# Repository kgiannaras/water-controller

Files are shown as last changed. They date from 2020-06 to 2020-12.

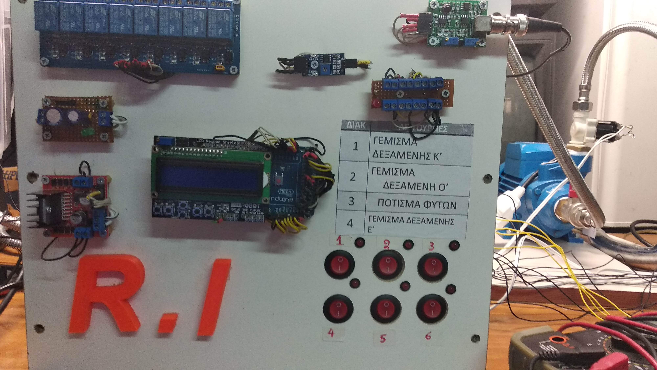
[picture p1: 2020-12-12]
photo/IMG_20200913_190725.jpg

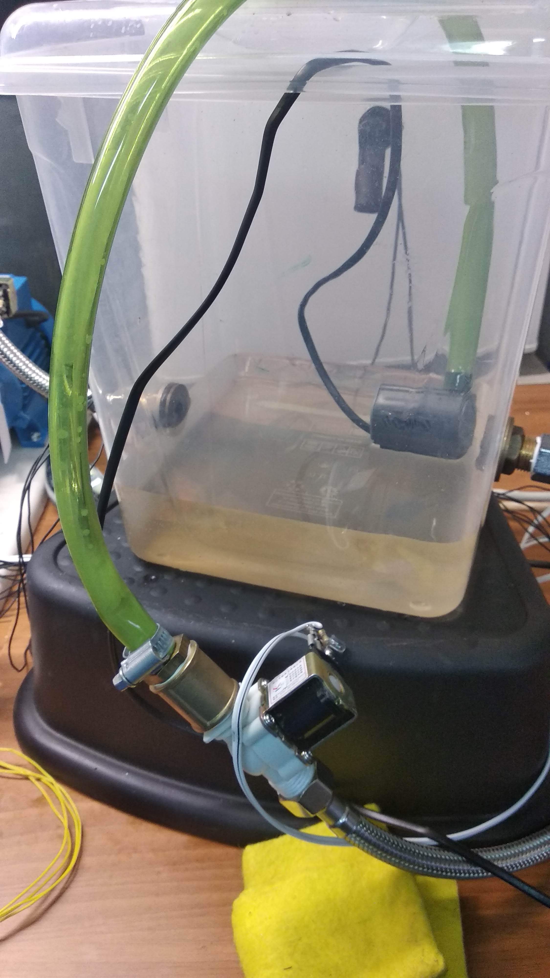
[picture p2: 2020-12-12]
photo/IMG_20200913_191104.jpg

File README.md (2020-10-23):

ΠΕΡΙΛΗΨΗ

Ο σκοπός της ομάδας μας για φέτος, είναι η δημιουργία  ενός συστήματος, το οποίο θα συλλέγει το νερό της βροχής σε μια δεξαμενή και αφού ελέγχει την οξύτητα του, θα το διαχειρίζεται ανάλογα. Αν είναι ακατάλληλο, το αποθηκεύει σε μια δεξαμενή, όπου θα κριθεί από τον κάτοχο το τι θα το κάνει. Ενώ, αν είναι κατάλληλο το νερό,  το αποθηκεύει προς χρήση είτε μέσω των διασωληνώσεων του σπιτιού(π.χ θερμοσίφωνας, βρύση,κ.λ.π), είτε μέσω μιας διασωλήνωσης, για άλλου είδους χρήση. Στην δική μας περίπτωση, το κατάλληλο νερό, το αξιοποιήσαμε σε κάτι που θεωρούμε πολύ σημαντικό, την αστική γεωπονία. Το σύστημα που προτείνουμε έχει ως κύρια πλεονεκτήματα την εξοικονόμηση από 30 έως 50 τις εκατό του πόσιμου νερού με οικονομικό, αλλά και περιβαντολλογικό όφελος και στην περίπτωση της αστικής καλλιέργειας προσφέρει την βέλτιστη ανάπτυξη των φυτών και είναι ό,τι καλύτερο όσον αφορά την αστική γεωπονία.Τα υλικά που θα χρησιμοποιήσουμε για την δημιουργία αυτής της κατασκευής, είναι τα παρακάτω:

ΗΛΕΚΤΡΟΝΙΚΑ

1x Arduino Mega                                    23.90 ΕΥΡΩ
1x Σταθεροποιημένο τροφοδοτικό 12V/5A               9.00 ΕΥΡΩ
1x Σταθεροποιημένο τροφ. 12V / 2A                   3.00 ΕΥΡΩ
2x  HC-SR04                                         5.00 ΕΥΡΩ
1x  8 relay                                         4.44 ΕΥΡΩ
1x  D1 ROBOT LCD                                    2.55 ΕΥΡΩ
1x ph sensor    Liquid PH 0-14 Value Detect Sensor 17,00 ΕΥΡΩ      
1x Water level sensor  Tank Pool Horizontal         2,77 ΕΥΡΩ

ΥΔΡΑΥΛΙΚΑ

4x  Ηλεκτροβάνες 12V Solenoid Valve 1/2"  60.00ΕΥΡΩ
3x  Μπιτόνια                              30.90ΕΥΡΩ
3χ βρυσάκια διακοπτης                    12.00 ΕΥΡΩ
2x  Σπιράλ 25cm                           4.00 ΕΥΡΩ
2x  Σπιράλ 60cm                           4.50 ΕΥΡΩ
5x  Μαστοί                               12.50 ΕΥΡΩ
1x teflor                                 0,30 ΕΥΡΩ
Συνολική Αξία:                         191 ,86 ΕΥΡΩ

Αναλυτική περιγραφή όλων των βημάτων υλοποίησης υπάρχουν στην ιστοσελίδα μας
https://openedtech.ellak.gr/robotics2020/sillektis-elegktis-oxinis-vrochis/

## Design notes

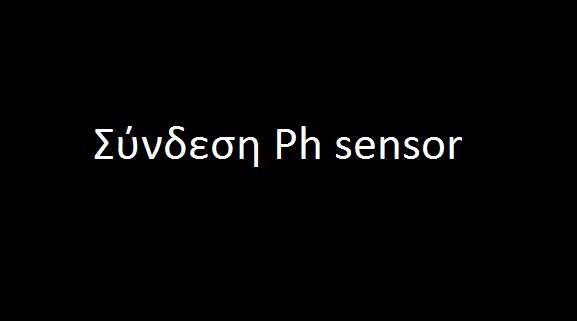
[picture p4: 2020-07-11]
photo/Σύνδεση-Ph-sensor.png

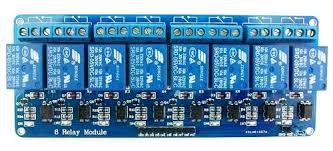
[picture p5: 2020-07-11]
photo/8r.jpg

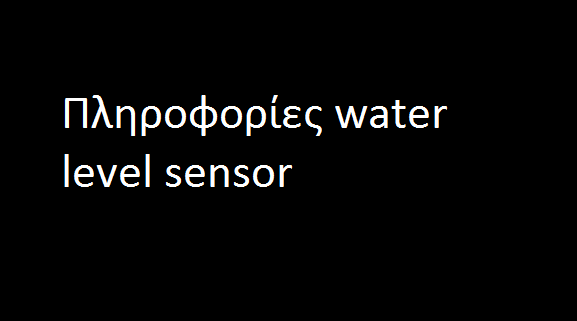
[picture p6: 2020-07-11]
photo/πληροφοριες-water-level.png

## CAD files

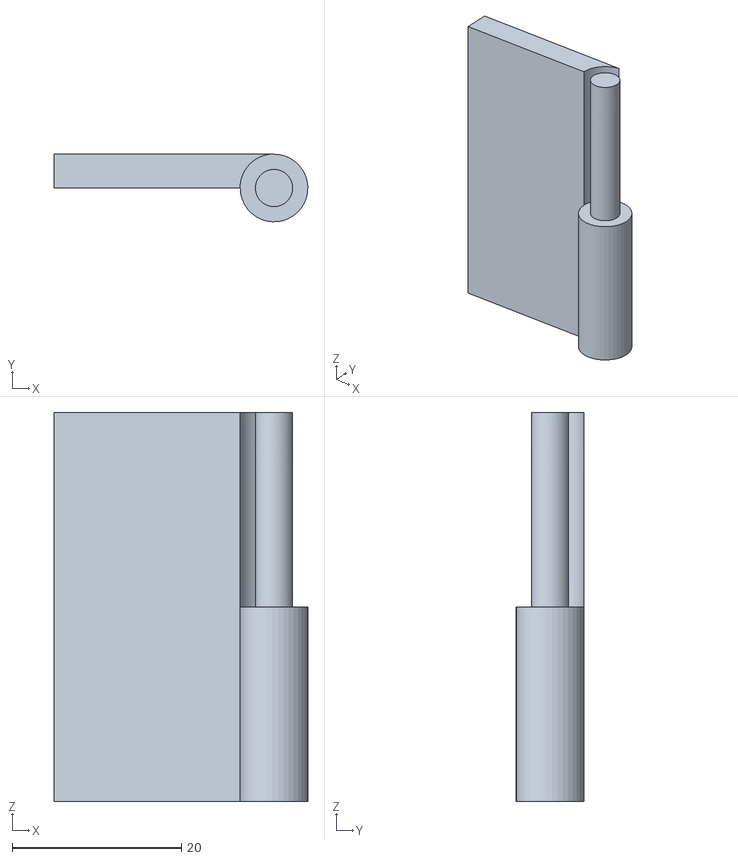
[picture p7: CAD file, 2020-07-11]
stl/hingecomplete.stl
30.0 x 7.99 x 46.0

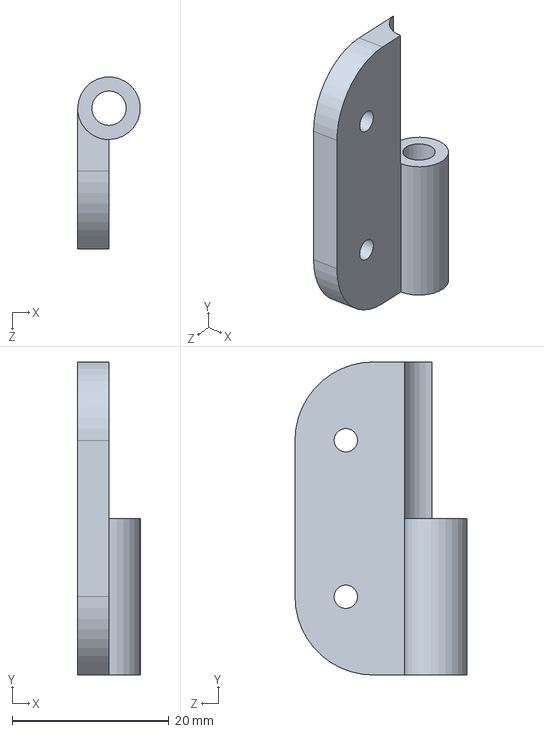
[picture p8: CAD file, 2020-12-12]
123d/Quick_Hinge/long-hinge-pt2.SLDPRT
7.99 x 40.0 x 22.0 mm

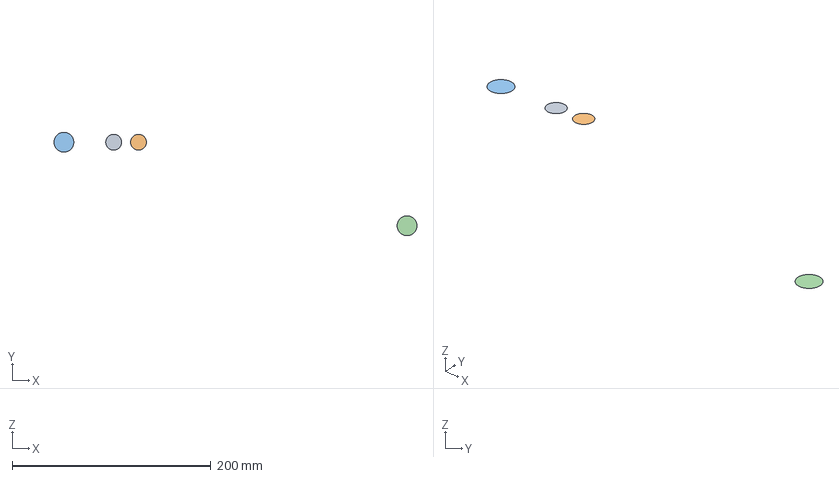
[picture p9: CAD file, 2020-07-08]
freecad/tank_o.FCStd
365.0 x 104.0 x 0 mm
Circle
Circle001
Circle002
Circle003

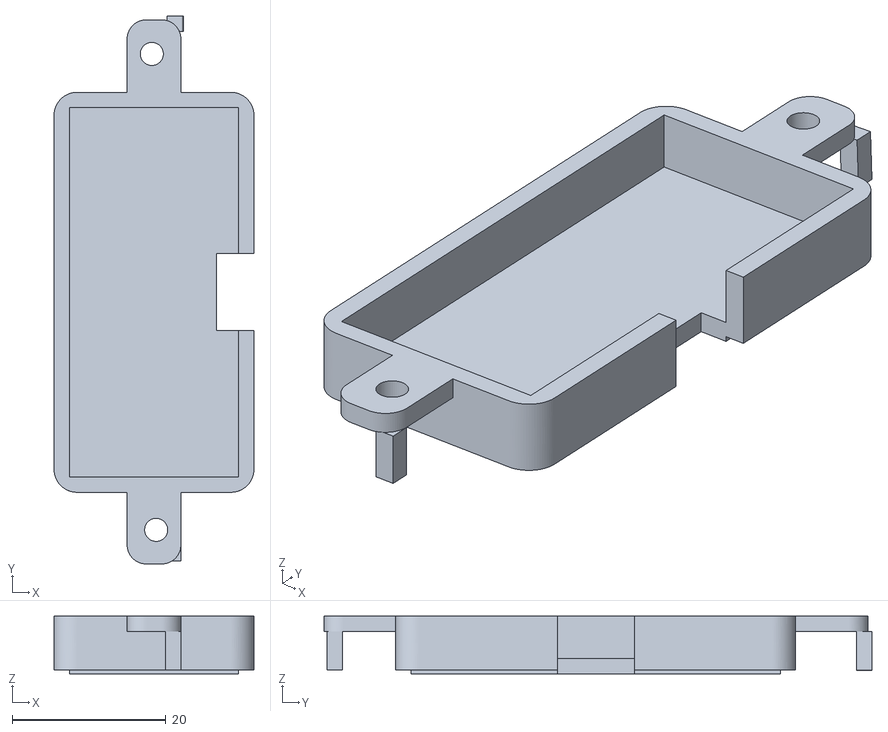
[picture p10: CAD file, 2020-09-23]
stl/hcsr04case.stl
26.0 x 71.2 x 7.50

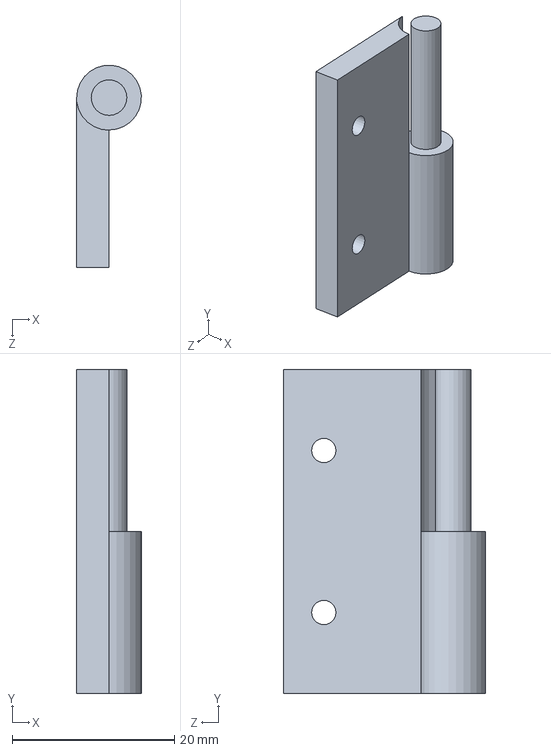
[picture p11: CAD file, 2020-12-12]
123d/Quick_Hinge/long-hinge-pt1.SLDPRT
7.99 x 40.0 x 25.0 mm

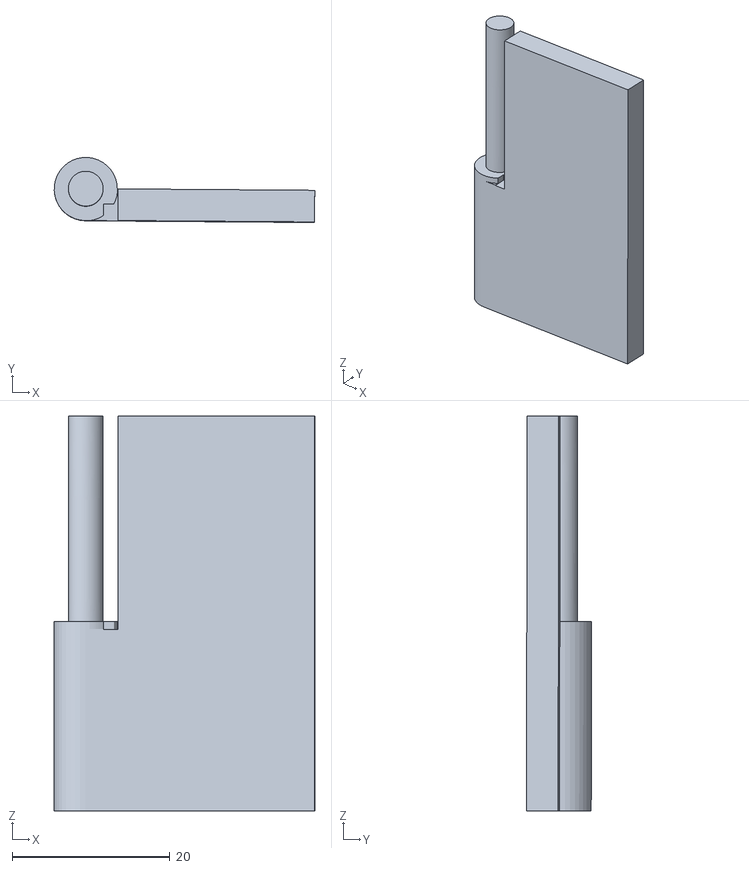
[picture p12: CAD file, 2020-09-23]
stl/hingeall.stl
33.0 x 8.24 x 50.0

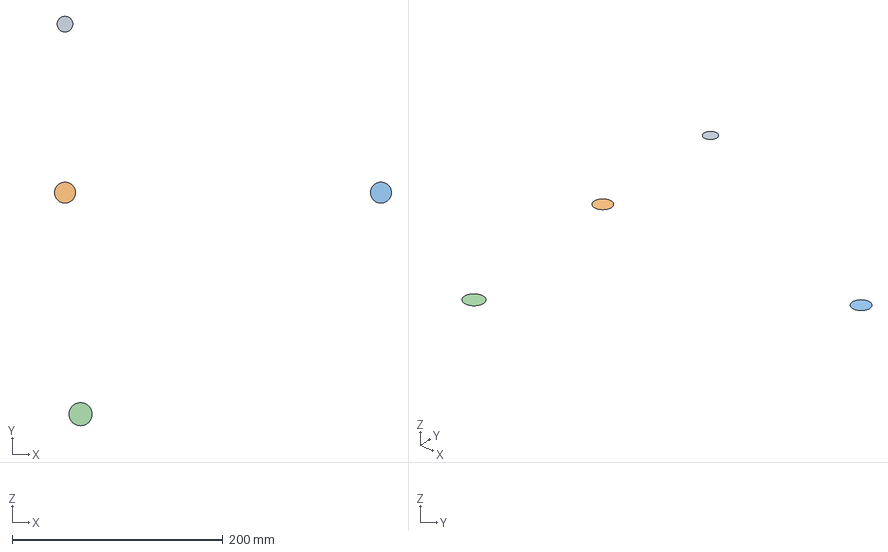
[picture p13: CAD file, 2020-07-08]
freecad/tank_e.FCStd
320.0 x 388.9 x 0 mm
Circle
Circle001
Circle002
Circle003

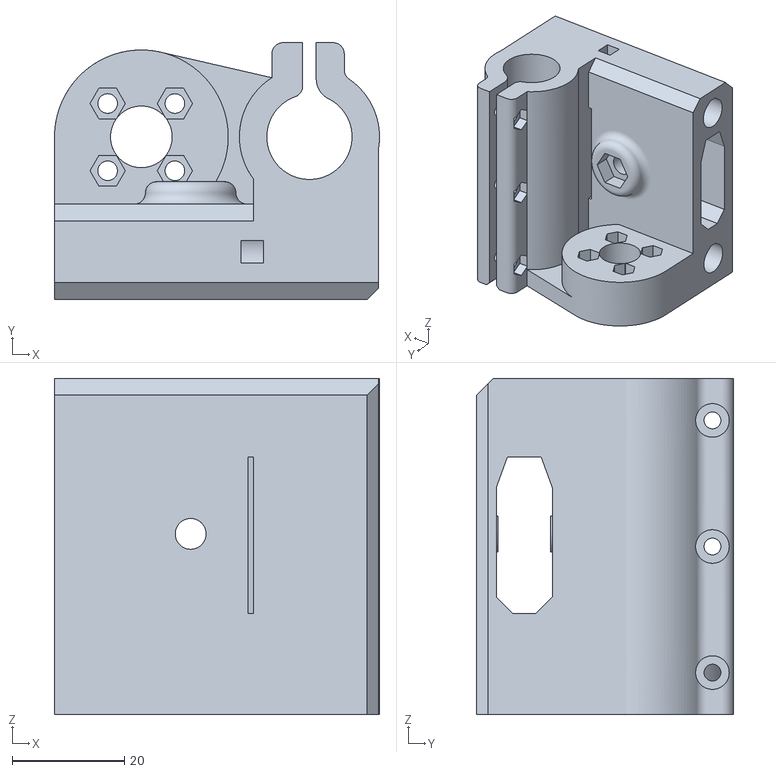
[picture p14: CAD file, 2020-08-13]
stl/x_end_idler.stl
58.0 x 45.8 x 60.0

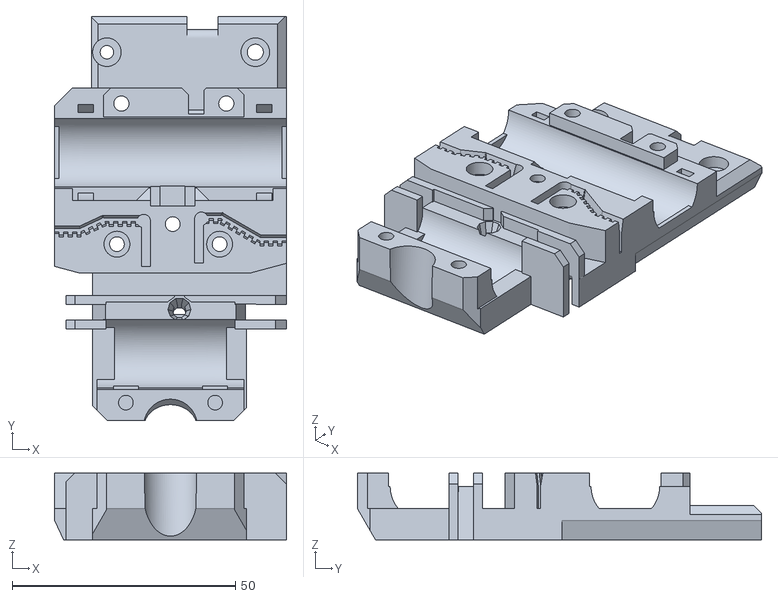
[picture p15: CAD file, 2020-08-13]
stl/X-carriage(R2)-MK3s_MK3s.stl
52.0 x 90.5 x 15.0

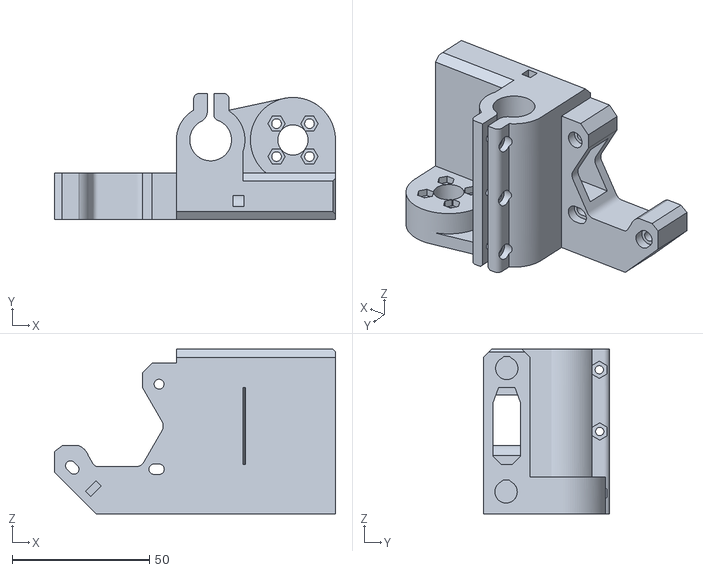
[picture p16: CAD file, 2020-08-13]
stl/x_end_motor.stl
102.4 x 46.0 x 60.0

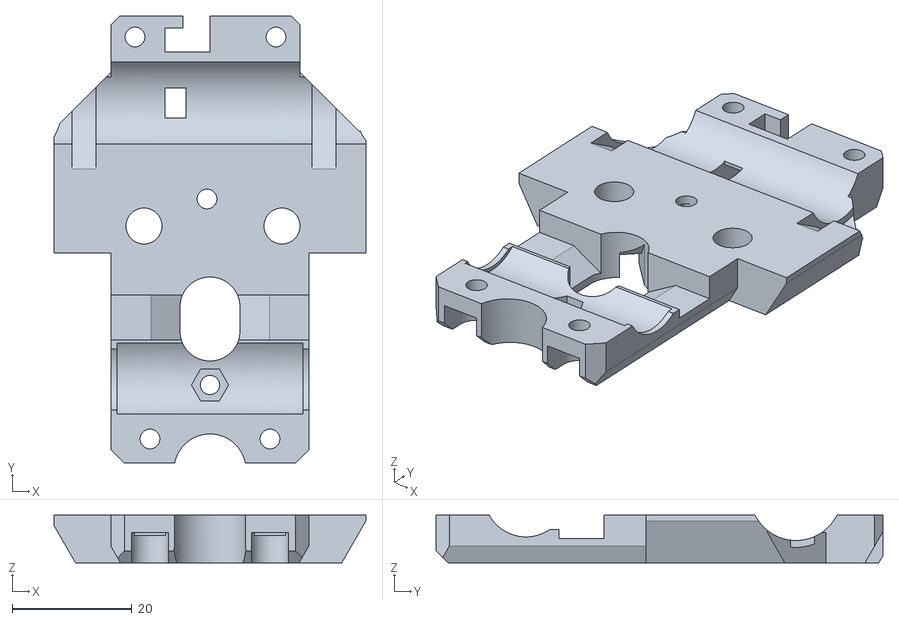
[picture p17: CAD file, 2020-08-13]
stl/Prusa X-Carriage Rear (R3).stl
52.0 x 74.5 x 8.00

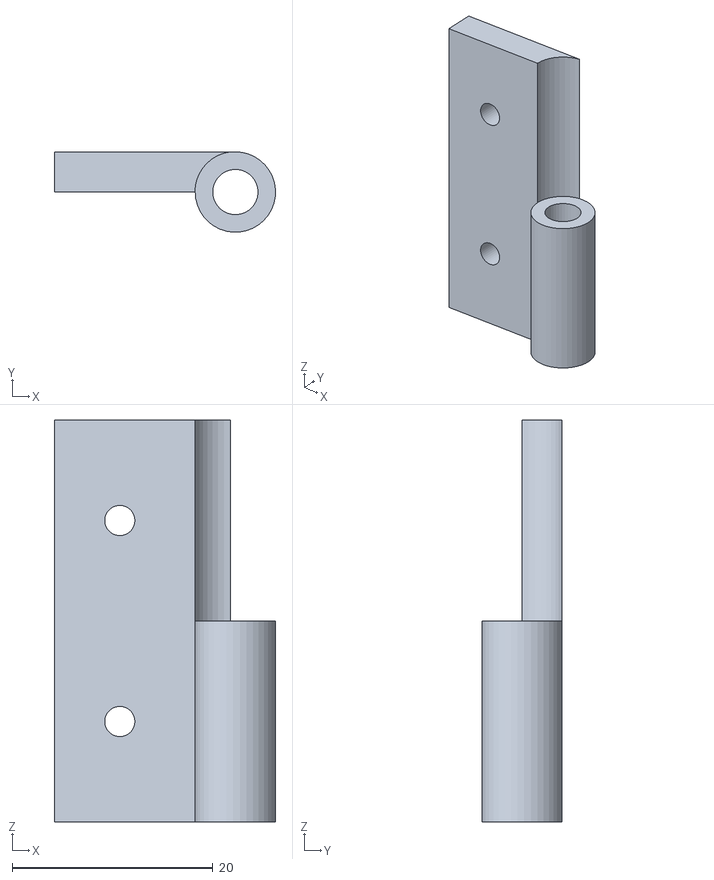
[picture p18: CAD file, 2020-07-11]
stl/long-hinge-pt2.STL
22.0 x 7.99 x 40.0

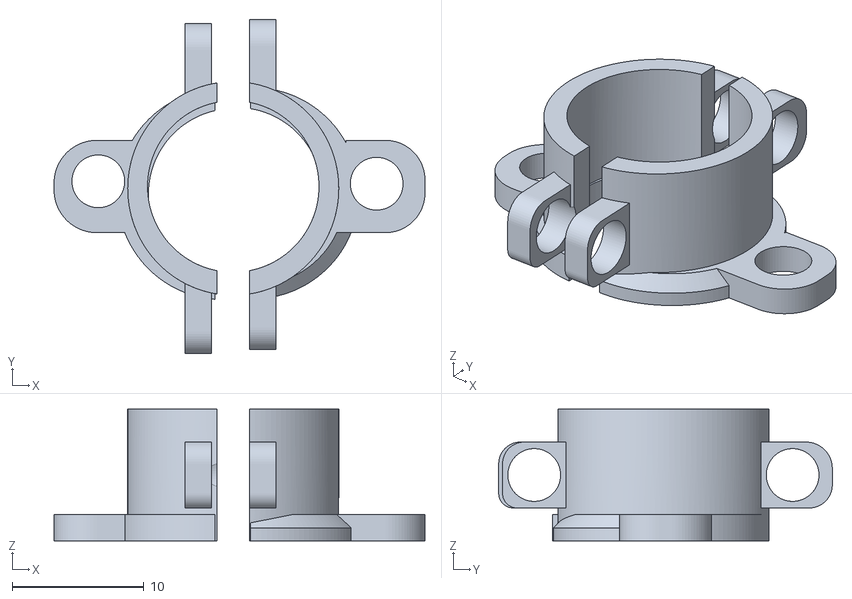
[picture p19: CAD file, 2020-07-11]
stl/ringPH.stl
28.1 x 25.3 x 10.0

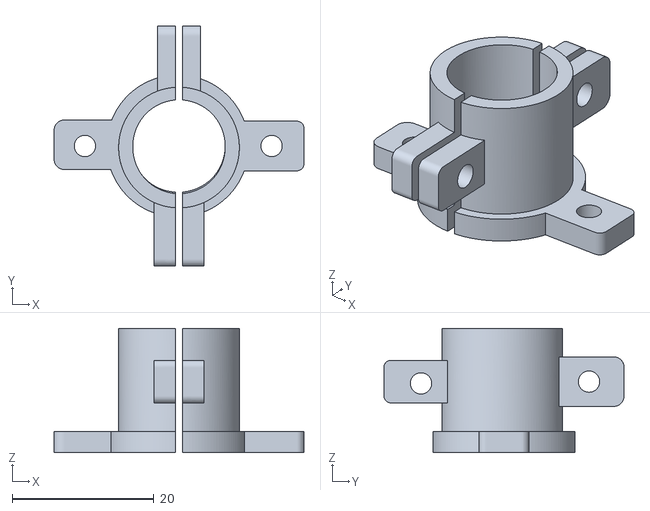
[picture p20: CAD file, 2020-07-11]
stl/ringell2.stl
35.2 x 33.8 x 17.5

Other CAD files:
stl/long-hinge-pt1.STL
stl/hingeup.stl
stl/hingebase.stl

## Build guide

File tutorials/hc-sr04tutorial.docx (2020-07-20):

Δημιουργία θήκης hc-sr04 (εύκολη εκδοχή)

Η θήκη είναι χωρισμένη σε δύο μέρη το καπάκι και την βάση

ΒΑΣΗ

Κατεβάζουμε το αρχείο από την παρακάτω ιστοσελίδα και μόλις το αποσυμπιέσουμε ανοίγουμε το long hinge pt2

Ιστοσελίδα (https://www.thingiverse.com/thing:47591)

Μόλις ανοίξουμε το αρχείο το επιλέγουμε και θα χρησιμοποιήσουμε την εντολή convert mesh to solid που θα μας επιτρέψει να τροποποιούμε το σχήμα γιατί αν δεν χρησιμοποιήσουμε την εντολή αυτή δεν θα μπορέσουμε να κάνουμε τίποτα στο σχήμα.

Με την εντολή sketch rectangle θα φτιάξουμε ένα ορθογώνιο 14mm x 40mm

Με την εντολή extrude υψώνουμε το σχήμα για 4mm .

Με την εντολή move το μετακινούμε εκεί που αρχίζει το ορθογώνιο του μεντεσε

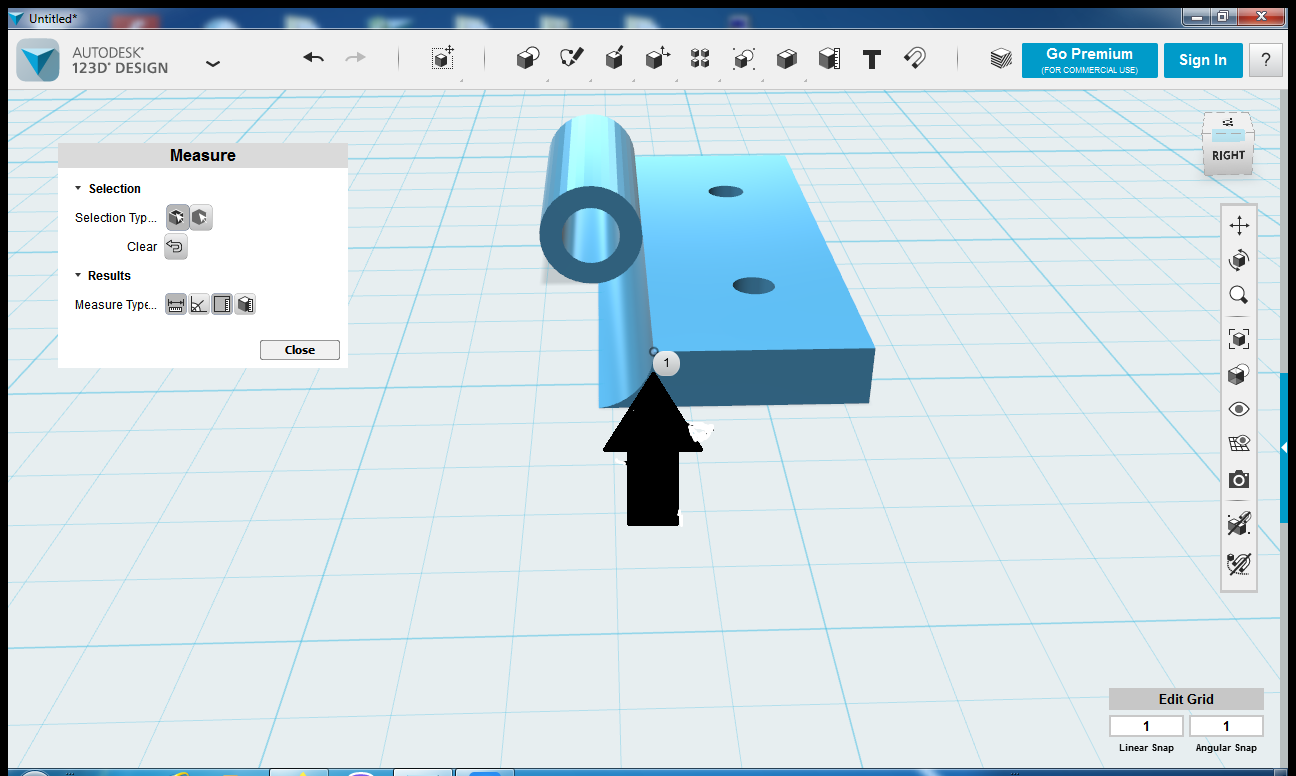
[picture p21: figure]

Έπειτα πηγαίνουμε στις επιλογές στο combine και επιλέγουμε το subtract θα χρειαστούν δυο επιλογές το πρώτο κλικ θα είναι στο το αντικείμενο που θέλουμε να ανοίξουμε την τρύπα και το δεύτερο κλικ στο το δεύτερο αντικείμενο που το σχήμα του θα σχηματίσει την τρύπα στο προηγούμενο αντικείμενο.Αυτό θα το κάνουμε μόνο που αντί για κύβο θα έχουμε τον μεντεσε και κύκλο το ορθογώνιο που φτιάξαμε . Στις επόμενες εικόνες φαίνεται ένα παράδειγμα ενός κύβου από τον οποίο θα αφαιρέσουμε ένα μέρος μιας σφαίρας.

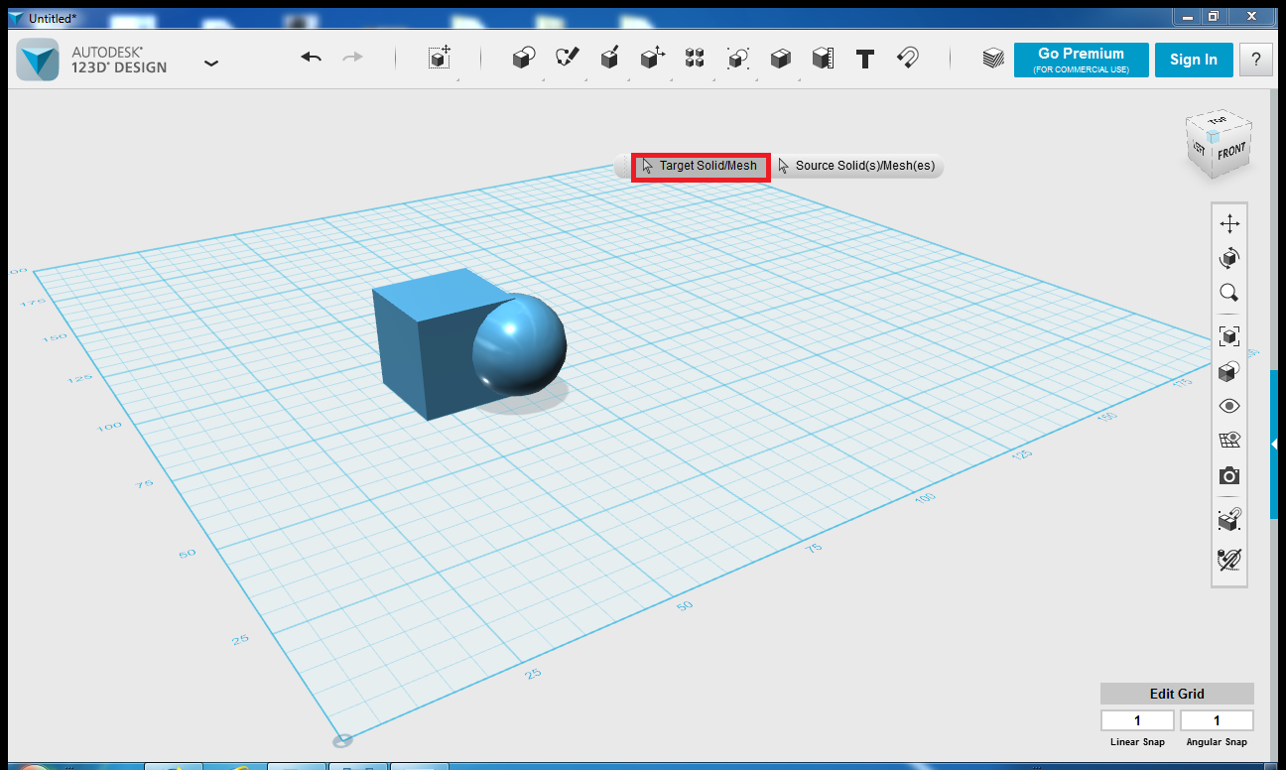
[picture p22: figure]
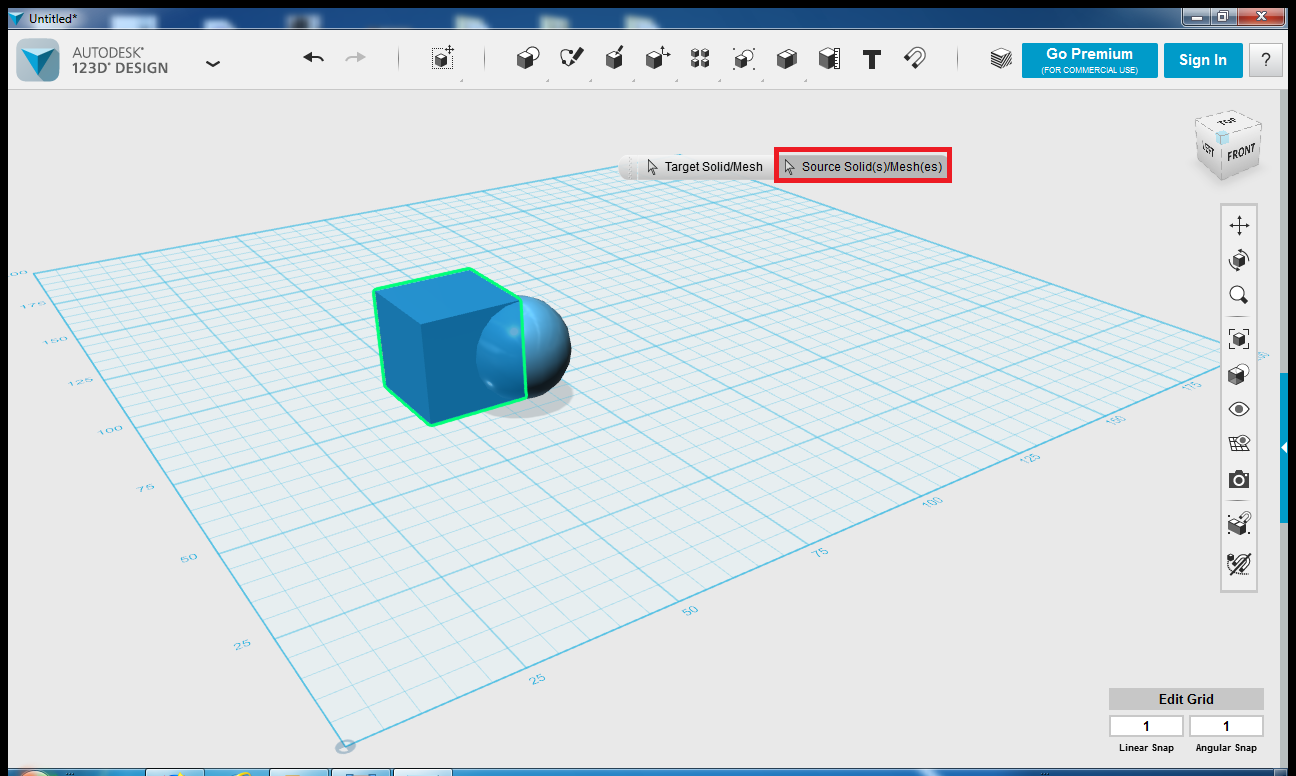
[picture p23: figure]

Στην επόμενη εικόνα φαίνεται το τελικό σχήμα που απέμεινε μετά την αφαίρεση του δεύτερου αντικειμένου

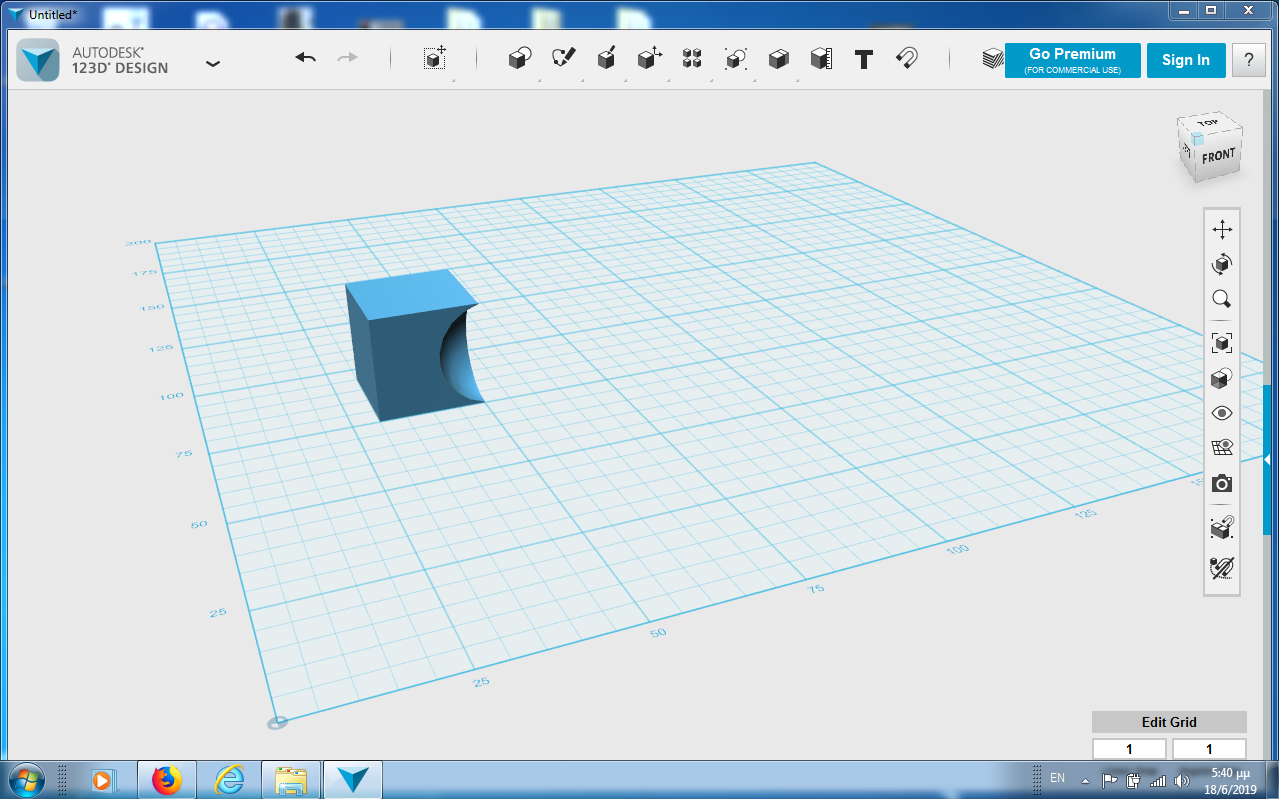
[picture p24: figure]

Μόλις γίνει αυτό να μεγαλώσετε και τις δύο πλευρές εξωτερικά κατά 7mm με το extrude και αν τις μειώσετε εσωτερικά κατά 5mm με το extrude .

Με την εντολή sketch rectangle θα φτιάξουμε δύο ορθογώνια 2mm x 21mm

Με την εντολή extrude υψώνουμε το σχήμα για 4mm .

Με την εντολή move το μετακινούμε στις άκρες του μεντεσε

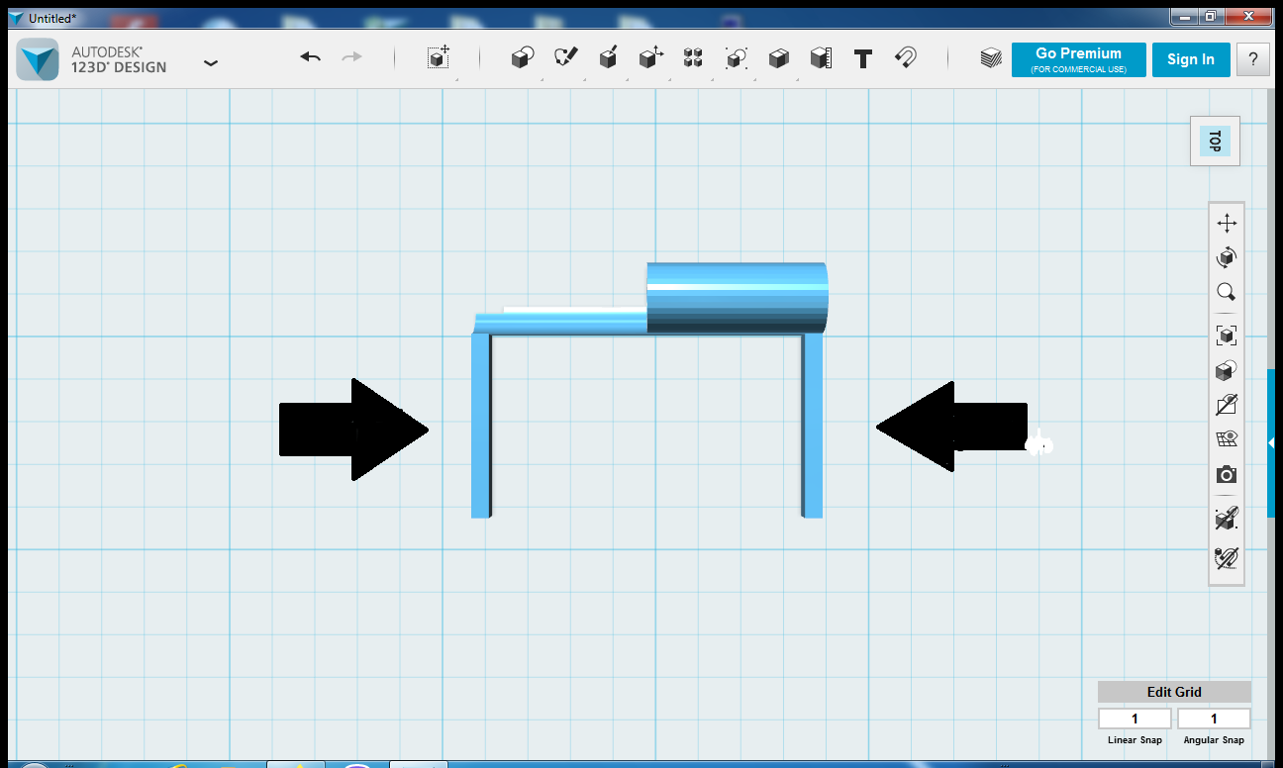
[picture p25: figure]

Στις λειτουργίες combine θα επιλέξουμε το merge και θα επιλέξουμε τα δύο αντικείμενα που θέλουμε να ενώσουμε το ένα ορθογώνιο με τον μεντεσε . Μόλις το κάνουμε ξανακάνουμε merge με το άλλο ορθογώνιο .

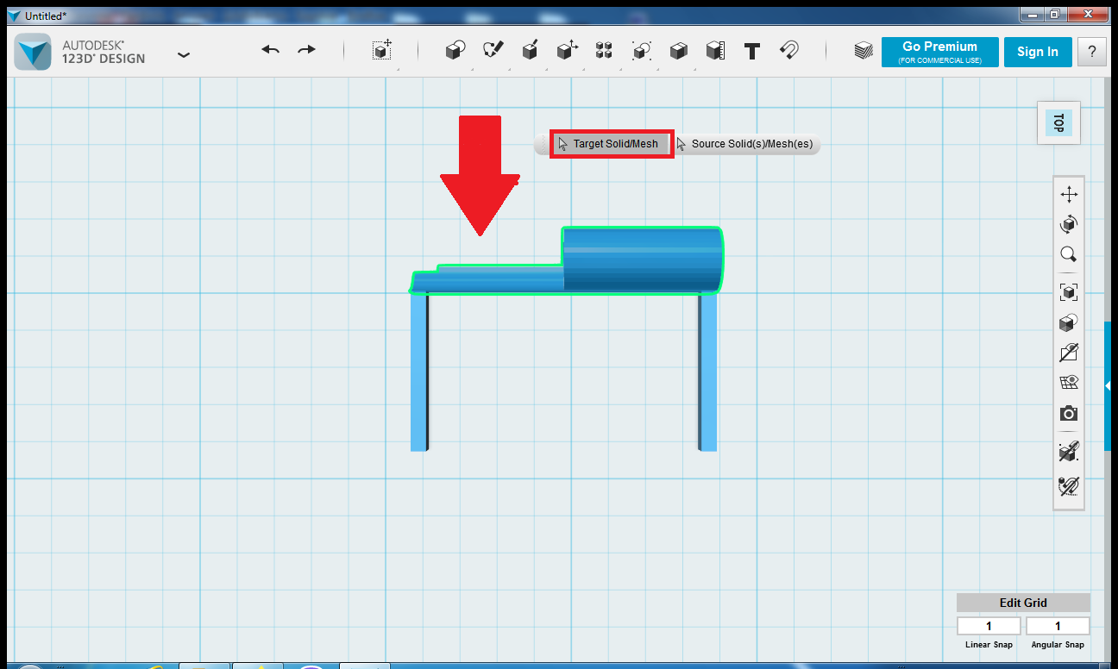
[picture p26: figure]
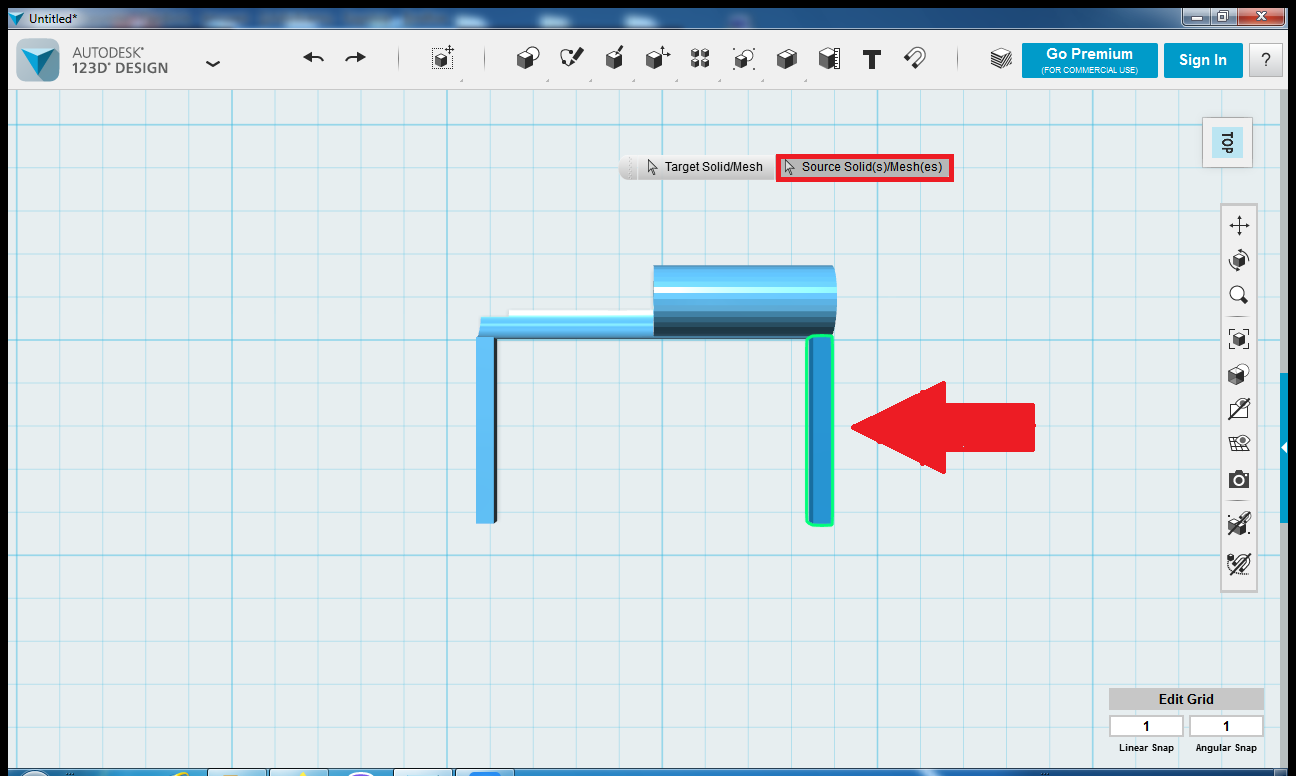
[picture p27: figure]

Με την εντολή sketch rectangle φτιάχνουμε ένα ορθογώνιο 50mm x 4mm

Με την εντολή extrude το υψώνουμε για 4mm .

Με την εντολή move μετακινούμε το ορθογώνιο στην άλλη πλευρά του μεντεσέ και να είναι κάθετος προς τις άλλες δύο πλευρές του μεντεσέ .

Μόλις το κάνετε αυτό θα κάνετε δύο τρύπες με το τρυπάνι των 2mm στα σημεία που δείχνει το αρχείο ώστε να βιδώσουμε την βάση.

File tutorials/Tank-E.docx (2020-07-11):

Δεξαμενή Ε΄

Η δεξαμενή Ε΄είναι η δεξαμενή στη οποία θα γίνεται η συλλογή του βρόχινου νερού και θα ξεχωρίζετε σε καθαρό ή όξινο ανάλογα με το ph.

Παρακάτω ακολουθούν οι πίνακες με τα αναγκαία υλικά και εργαλεία.

Υλικά για αυτό το βήμα | Ποσότητες
Ph sensor | 1
Water level sensor | 1
Μαστοί δεξαμενής | 2
Ηλεκτροβάνες | 2
Σπιράλ 25cm | 2
Σπιράλ 60cm | 2
Βρυσάκι διακόπτης | 2
3d δαχτυλίδι για τον ph | 1

Απαραίτητα εργαλεία για το βήμα αυτό

1) Δράπανο ηλεκτρικό
2) Ποτηροτρύπανο 15mm
3) Ποτηροτρύπανο 20mm
4) Ποτηροτρύπανο 22mm

5)Ποτηροτρύπανο 16mm

6)Κάβουρας για σύσφιξη μαστού

Βήμα 1: 1η πλευρά

Πρώτο βήμα είναι να ασχοληθούμε με την πρώτη πλευρά. Βάση του σχεδίου κάνουμε μία τρύπα 15mm που θα απέχει 50mm από το ανώτερο σημείο της δεξαμενής και θα απέχει 100mm από την αριστερή πλευρά της δεξαμενής. Αυτή η τρύπα θα γίνει χρησιμοποιώντας το ηλεκτρικό δραπανο και το ποτηροτρύπανο των 15mm.

Αν δεν γνωρίζετε τι είναι το ποτηροτρύπανο

Ακολουθεί ενδεικτική εικόνα.

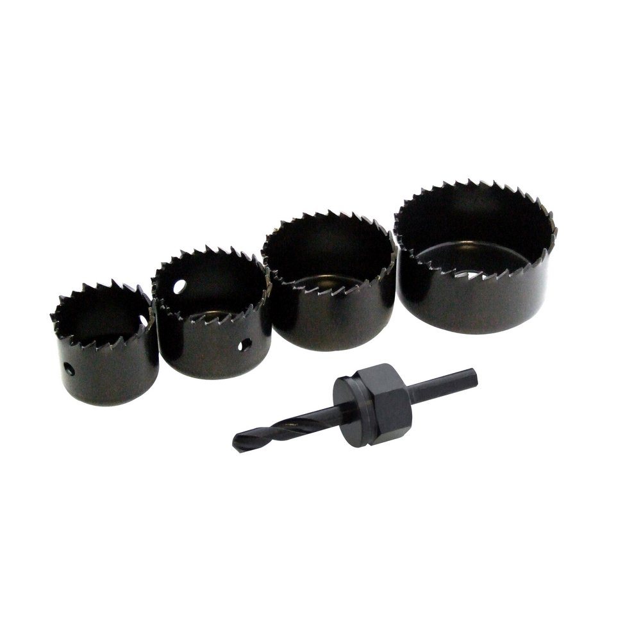
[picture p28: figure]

Εικόνα 1: Ποτηροτρύπανα

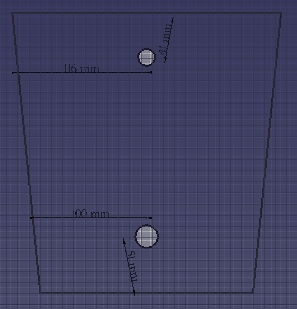
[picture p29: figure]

Εικόνα 2 :Σχέδιο πλευράς 1

Η παρακάτω εικόνα δείχνει το αποτέλεσμα της τρύπας.

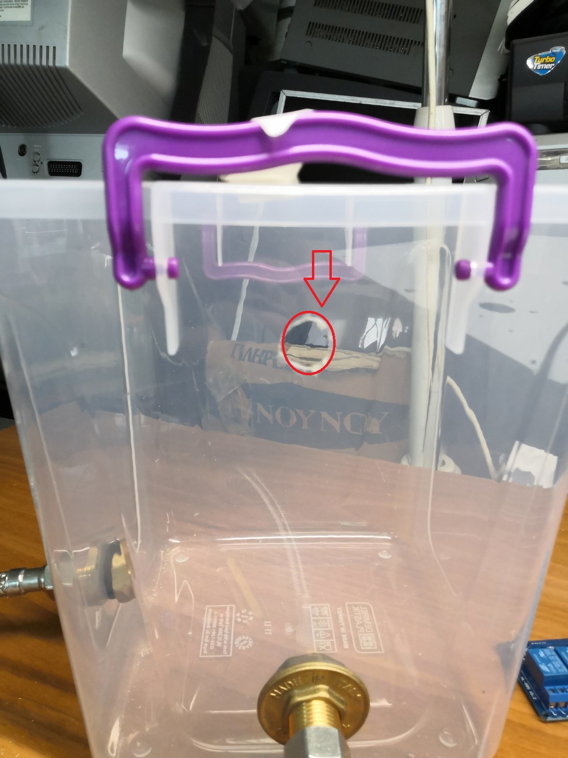
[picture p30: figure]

Εικόνα 3: Αποτέλεσμα τρύπας.

Στην ίδια πλευρά ανοίγουμε βάση του σχεδίου μία τρύπα 20mm που θα απέχει 50mm από την βάση και 100mm από αριστερά για να βάλουμε τον μαστό δεξαμενής. Αυτή η τρύπα θα χρειαστεί το ηλεκτρικό δράπανο και το ποτηροτρύπανο των 20mm.

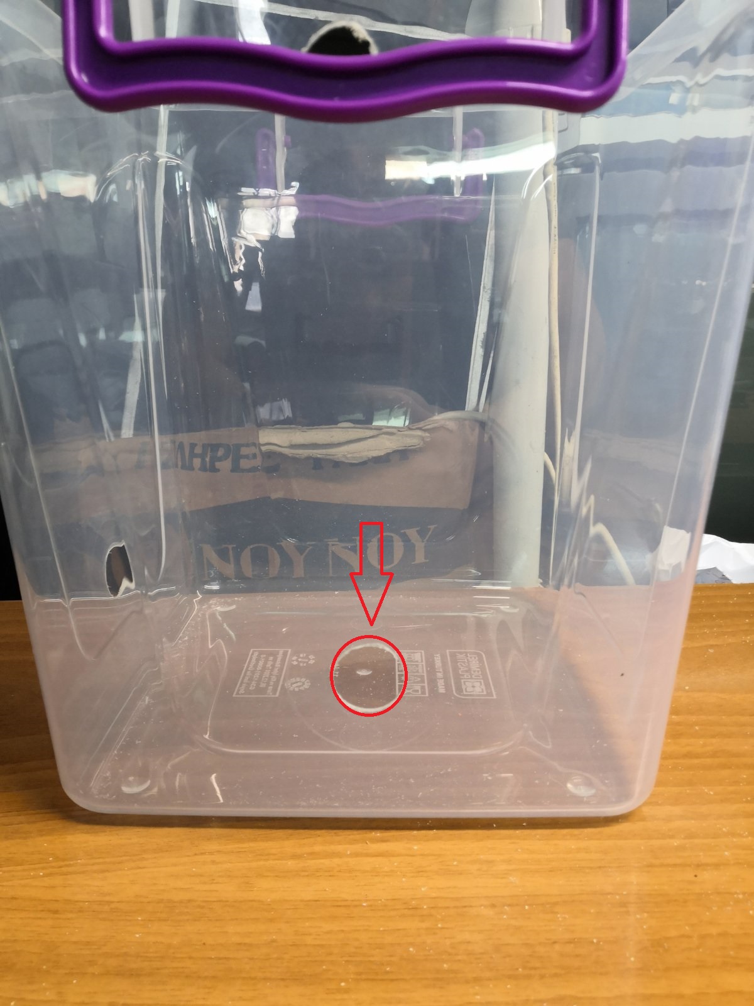
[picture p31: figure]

Εικόνα 4: Αποτέλεσμα τρύπας

Μόλις γίνουν και οι δύο τρύπες αρχίζουμε να συναρμολογουμε όλη την πλευρά. Αρχίζοντας από τον water level sensor πρώτα θα τον περάσουμε από μέσα με την ροδέλα και αργότερα θα περάσουμε από έξω το παξιμάδι του.

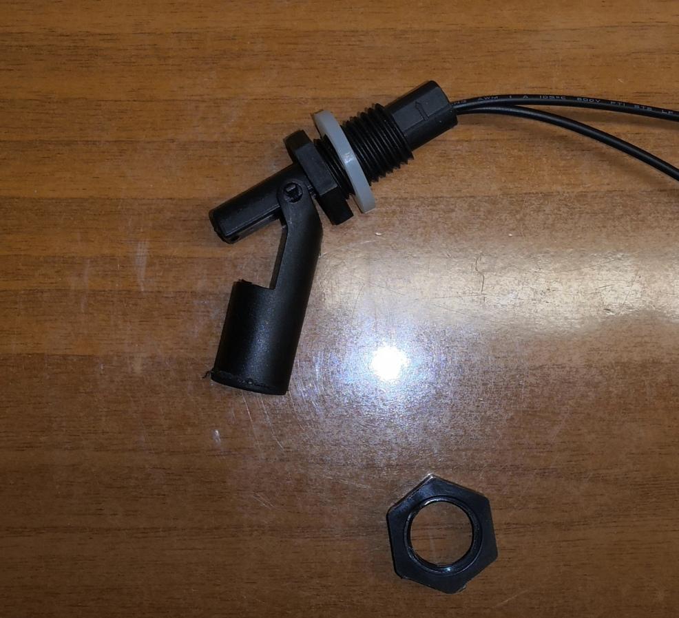
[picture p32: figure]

Εικόνα 5: Water level sensor και παξιμάδι.

Αργότερα θα περάσουμε τον μαστό δεξαμενής. Προσοχή η λαστιχένια ροδέλα θα μπεί από μέσα και το παξιμάδι από έξω για να μην υπάρξουν διαρροές .

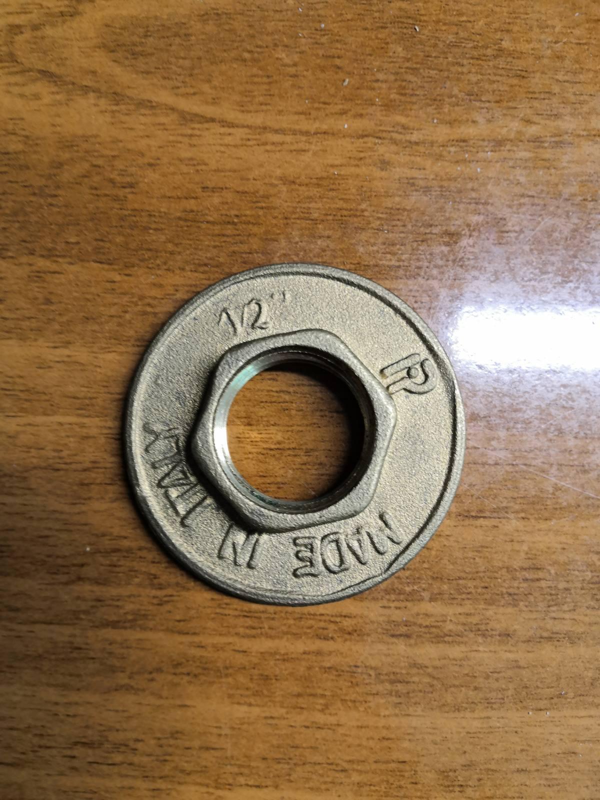
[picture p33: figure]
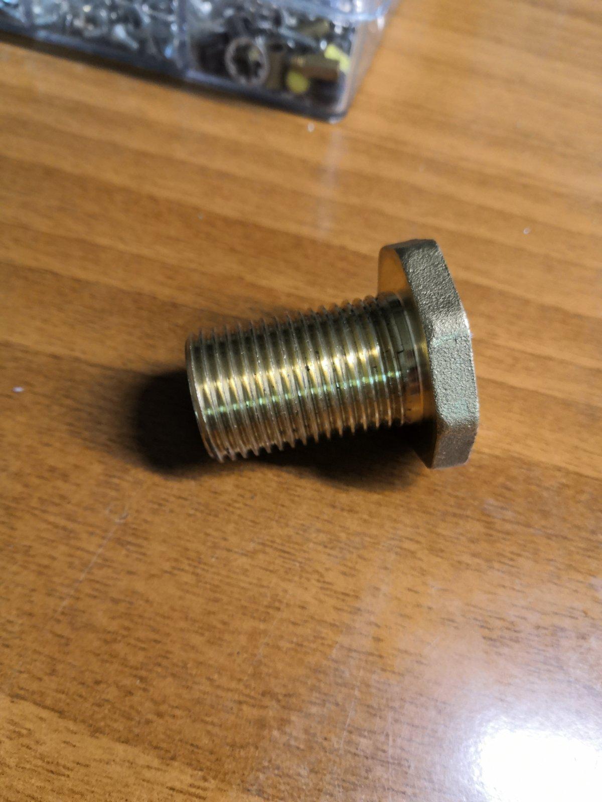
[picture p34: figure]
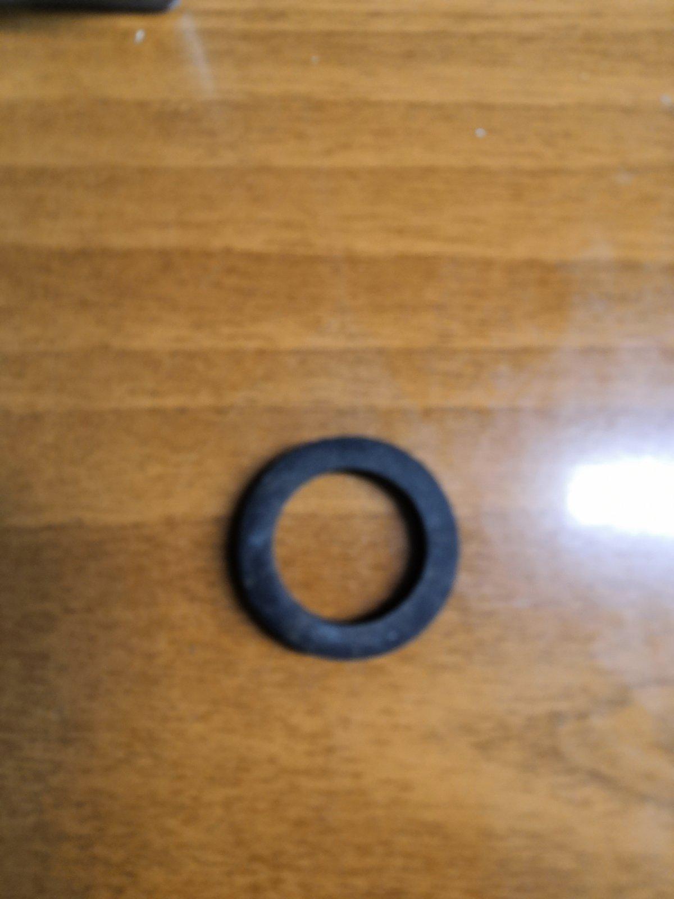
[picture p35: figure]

Εικόνα 6: Μαστος δεξαμενής, παξιμάδι και ροδέλα.

Βήμα 2: Καπάκι

Μόλις γίνει αυτό θα ασχοληθούμε με το καπάκι για να βάλουμε τον ph sensor. Βάση του σχεδίου θα κάνουμε μια τρύπα 22mm που θα απέχει 120mm απο την δεξιά πλευρά του καπακιού και θα απέχει 120mm από την πάνω πλευρά του καπακιού. Αυτή η τρύπα θα γίνει χρησιμοποιώντας το ηλεκτρικό δραπανο και το ποτηροτρύπανο των 22mm.

Εικόνα 7: Σχέδιο καπακιού

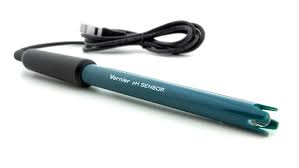
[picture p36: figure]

Εικόνα 8: Ph sensor

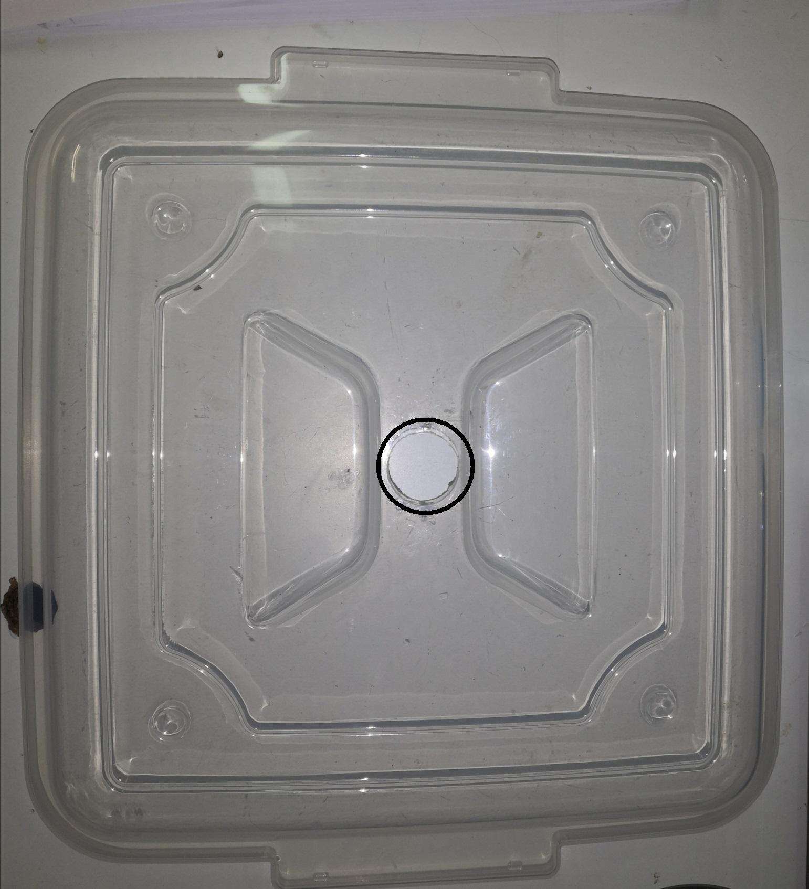
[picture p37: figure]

Εικόνα 9: Αποτέλεσμα τρύπας

Όμως επειδή το σχήμα του δικού μας ph sensor δεν είναι ομοιόμορφο χρειάστηκε να δημιουργήσουμε το παρακάτω 3d αντικείμενο ώστε να το εμποδίζει από να πέσει μέσα στην δεξαμενή.

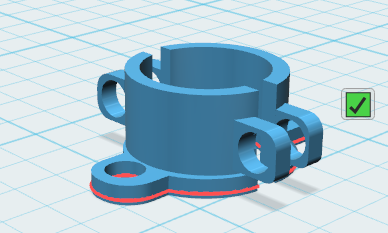
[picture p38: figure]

Εικόνα 10: 3d θήκη

Στο παρακάτω βίντεο εξηγούμε την τοποθέτησή του.

Βήμα 3: 2η πλευρά

Σε αυτό το βήμα θα ασχοληθούμε με την τρύπα ενός δεύτερου μαστού.Ανοίγουμε βάση του σχεδίου μία τρύπα 20mm που θα απέχει 50mm από την βάση και 100mm από αριστερά για να βάλουμε τον δεύτερο μαστό δεξαμενής.Αυτή η τρύπα θα γίνει χρησιμοποιώντας το ηλεκτρικό δραπανο και το ποτηροτρύπανο των 20mm.

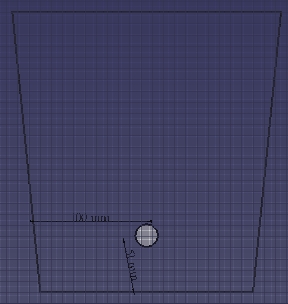
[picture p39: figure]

Εικόνα 11: Σχέδιο 2ης πλευράς

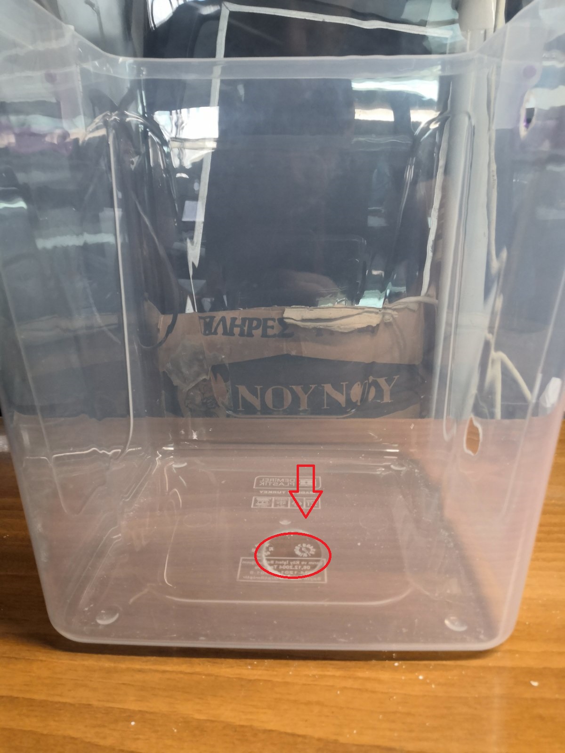
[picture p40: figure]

Εικόνα 12: Αποτέλεσμα τρύπας

Μόλις γίνει η τρύπα θα ενώσετε τον μαστό στην δεξαμενή όπως παραπάνω.

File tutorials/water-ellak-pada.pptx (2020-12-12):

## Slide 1

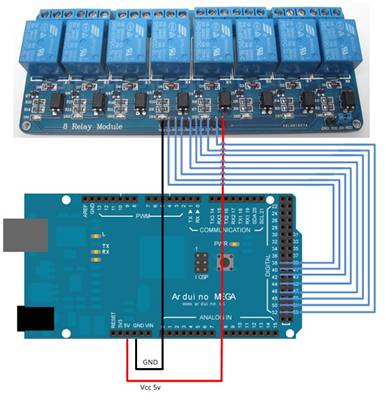
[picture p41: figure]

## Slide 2

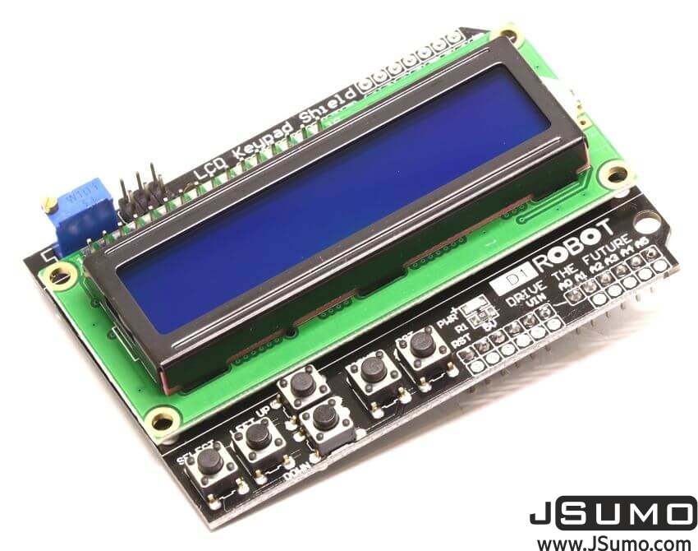
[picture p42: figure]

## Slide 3

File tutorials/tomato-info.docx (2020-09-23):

8. Ντομάτα

Το έδαφος για να είναι έτοιμο να δεχτεί το φυτό πρέπει να προετοιμαστεί έγκαιρα, κατάλληλα και επιμελημένα. Οι κυριότερες εργασίες που πρέπει να γίνουν είναι:

α) Προσεκτική απομάκρυνση των υπολειμμάτων της προηγούμενης καλλιέργειας, εντός και πέριξ του θερμοκηπίου και καταστροφή τους με φωτιά για να μειωθούν σημαντικά οι εστίες μόλυνσης, να διευκολυνθεί η κατεργασία του εδάφους και να είναι πιο αποτελεσματική η ηλιοαπολύμανση του εδάφους.

β) Επαρκής άρδευση με μπέκ υδρονέφωσης για να βλαστήσουν οι σπόροι των ζιζανίων και να νεκρωθούν τα νεαρά σπορόφυτα λόγω της ηλιοαπολύμανσης.

γ) Φρεζάρισμα και ισοπέδωση του εδάφους.

δ) Ενσωμάτωση της κοπριάς ή του κόμποστ στο έδαφος με τσουγκράνα ή με σκαπτικό πολύ γρήγορα και ισοπέδωση του εδάφους ξανά σε δόση 250 Kg / στρέμμα.

ε) Ηλιοαπολύμανση (κάλυψη της επιφάνειας του εδάφους για 4 - 6 εβδομάδες, με ειδικό φύλλο πλαστικού, το οποίο παραχώνεται στα άκρα του για να εγκλωβίζει την ηλιακή ενέργεια).

ζ) Βασική λίπανση στις γραμμές φύτευσης. Προστίθενται ανόργανα και οργανικά λιπάσματα. Στο εμπόριο κυκλοφορούν πολλά τέτοια λιπάσματα. Οι ποσότητες των κύριων θρεπτικών στοιχείων που θα προστεθούν για τη συμπλήρωση της γονιμότητας του εδάφους του θερμοκηπίου πρέπει να υπολογίζονται με βάση την ανάλυση του εδάφους.

η) Προστίθενται ωφέλιμοι μικροοργανισμοί με τη βασική λίπανση, όπως και νηματωδοκτόνα. Στο εμπόριο κυκλοφορούν διάφορα σκευάσματα ωφέλιμων μικροοργανισμών.

θ) Φρεζάρισμα και άνοιγμα αυλακιών.

Σπορά

Για την παραγωγή σποροφύτων τομάτας χρησιμοποιούνται ειδικοί καλυμμένοι χώροι (σπορεία) αποκλειστικά για το σκοπό αυτό, χωριστά από το θερμοκήπιο. Η έκταση του σπορείου υπολογίζεται σε 8-10% της έκτασης του θερμοκηπίου. Δηλαδή, για ένα στρέμμα θερμοκηπίου απαιτείται έκταση 80 - 100m2 σπορείου. Οι χώροι των σπορείων είναι ηλιοαπολυμασμένοι, χωρίς ζιζάνια (εντός και πέριξ). Στα παράθυρα και στις πόρτες τους υπάρχει εντομοστεγές δίκτυ, για να μειώνεται ο κίνδυνος μολύνσεων από το εξωτερικό περιβάλλον. Στην Κρήτη, πρακτικό ενδιαφέρον παρουσιάζουν τα σπορεία που ο χώρος τους έχει διαμορφωθεί σε πάγκους κατά τέτοιο τρόπο διατεταγμένους ώστε να διευκολύνεται ο έλεγχος των φυταρίων και οι καλλιεργητικές φροντίδες. Οι πάγκοι είναι συνήθως ξύλινοι, έχουν ύψος 80 - 100cm και πλάτος 80 - 150cm, περίπου. Μπορεί αντί για ξύλο να χρησιμοποιηθεί μεταλλικό δίχτυ ή πλαστικό προσαρμοσμένο σε ξύλινο πλαίσιο. Συνήθως εφαρμόζονται δύο τρόποι σποράς: Στον πρώτο, η σπορά γίνεται σε κιβώτια και στη συνέχεια τα φυτά μεταφυτεύονται σε πλαστικά κύπελλα ή ομαδικά μέσα σποράς. Στον δεύτερο, η σπορά γίνεται απ’ευθείας στα πλαστικά κύπελλα ή ομαδικά μέσα σποράς. Στην πράξη προτιμάται ο πρώτος τρόπος, γιατί επιτυγχάνεται καλύτερο και ομοιόμορφο φύτρωμα των σπόρων, ελέγχονται και περιποιούνται τα νεαρά φυτά σωστότερα και αποτελεσματικότερα, διευκολύνεται η επιλογή για μεταφύτευση των καλύτερων, υγιέστερων και πλέον ομοιόμορφων φυτών και περιορίζονται στο ελάχιστο οι απώλειες και τα έξοδα παραγωγής σποροφύτων.

Φύτευση

Φύτευση στο θερμοκήπιο: Η φύτευση στο θερμοκήπιο γίνεται περίπου 25 - 40 ημέρες από την μεταφύτευση στα κύπελλα ή στα ομαδικά μέσα σποράς. Επιλέγονται εύρωστα φυτά, ομοιόμορφα και καλής ανάπτυξης. Οι αποστάσεις φύτευσης καθορίζονται από διάφορους παράγοντες {π.χ. η εποχή φύτευσης, ο τύπος του θερμοκηπίου, το σύστημα άρδευσης, η καλλιεργούμενη ποικιλία και το σύστημα μόρφωσης που εφαρμόζεται (στο μονοστέλεχο σύστημα η φύτευση είναι πιο πυκνή ενώ στο διστέλεχο πιο αραιή). Στην Κρήτη συνηθίζεται η φύτευση να γίνεται σε διπλές γραμμές και οι αποστάσεις φύτευσης διαφέρουν ανάλογα την εποχή φύτευσης.

Καταπολέμηση ζιζανίων

Πολλά ζιζάνια μπορούν να ληφθούν υπόψη ως δείκτες σχετικά με την κατάσταση του εδάφους και έτσι να επέμβουν ανάλογα. Έτσι το ζιζάνιο Fumaria officinalis (καπνόχορτο) σχετίζεται με έδαφος με μεγάλη υγρασία, το Erodium cicutarium (χτενάκι) σχετίζεται με ξηρό και πετρώδες έδαφος, το Urtica urens (μικρή τσουκνίδα) σχετίζεται με ελαφρό και χουμώδες έδαφος, το Chenopodium album (λουβουδιά) σχετίζεται με έδαφος πλούσιο σε άζωτο, το Sinapis arvensis (βρούβα) σχετίζεται με αλκαλικό έδαφος (pH>7) και το Veronica officinalis (γαλαζάκι) σχετίζεται με όξινο έδαφος (pH<7). Ο κύριος στόχος είναι να κρατηθούν τα ζιζάνια σε τέτοιο επίπεδο που δεν θα δημιουργούν ανταγωνισμό στα φυτά. Ο έλεγχος τους επιτυγχάνεται με τα ακόλουθα προληπτικά μέτρα και βιολογικά μέσα. Τα κυριότερα προληπτικά μέτρα αντιμετώπισης των ζιζανίων είναι η χρησιμοποίηση σπόρου σποράς, κόμποστ, κοπριάς κ.λ.π απαλλαγμένα από σπόρους ή όργανα αγενούς αναπαραγωγής των ζιζανίων και ο επιμελημένος καθαρισμός των μηχανημάτων που χρησιμοποιήθηκαν σε μολυσμένες από ζιζάνια περιοχές πριν από τη χρήση τους σε μη μολυσμένες περιοχές.

Άρδευση

Λίπανση

Εκτός από τη βασική λίπανση, που γίνεται κατά την προετοιμασία του εδάφους, επιβάλλεται και η εφαρμογή επιφανειακών λιπάνσεων κατά την διάρκεια της ανάπτυξης και καρποφορίας των φυτών. Βασικό στοιχείο επιτυχίας μιας καλλιέργειας ντομάτας στο θερμοκήπιο, αποτελεί η έγκαιρη και ισορροπημένη λίπανση και άρδευση. Η εφαρμογή της επιφανειακής λίπανσης μπορεί να γίνει είτε με την απευθείας χρήση των στερεών λιπασμάτων (διασκορπισμός στην επιφάνεια-πότισμα ή ενσωμάτωση - πότισμα) ή μαζί με το νερό ποτίσματος ή με διαφυλλικές λιπάνσεις. Η πιο επιθυμητή και εύκολη προσέγγιση της επιφανειακής λίπανσης είναι η τροφοδοσία διαλυμάτων των λιπαντικών στοιχείων στο νερό ποτίσματος με τη βοήθεια ειδικών λιπαντήρων.

Κλάδεμα

Το κλάδεμα αποσκοπεί στην εξισορρόπηση βλάστησης και καρποφορίας, στον περιορισμό του αριθμού των ταξιανθιών στον κεντρικό μονοστέλεχο τύπο, στη συγκέντρωση της παραγωγής των φυτών σε ορισμένη χρονική περίοδο, στην εξασφάλιση ομοιογένειας των καρπών, στη βελτίωση της ποιότητας των καρπών (γεύση, συνεκτικότητα, χρώμα κ.ά), στη διευκόλυνση εκτέλεσης των καλλιεργητικών εργασιών, στη διευκόλυνση εκμετάλλευσης του χώρου του θερμοκηπίου από τα φυτά και διευκόλυνση επιθεώρησης της καλλιέργειας. Το κλάδεμα συνιστάται κυρίως στη αφαίρεση και κορυφολόγημα βλαστών, στην αφαίρεση φύλλων και στην αραίωση καρπών. Τα υλικά κλαδέματος μεταφέρονται έξω από το θερμοκήπιο όπου συνήθως κομποστοποιούνται, ενώ τα προσβεβλημένα παραχώνονται ή καταστρέφονται με φωτιά.

Υποστύλωση

Η υποστύλωση έχει ως σκοπό να διευκολύνει τα κλαδέματα και τα ξεφυλλίσματα των φυτών, την εκτέλεση των καλλιεργητικών φροντίδων, τον φυσικό και τεχνητό αερισμό και συντελεί στον καλύτερο φωτισμό των φυτών. Η ντομάτα στο θερμοκήπιο αναπτύσσεται κατακόρυφα, γιατί γίνεται καλύτερη εκμετάλλευση του χώρου στο θερμοκήπιο. Η υποστύλωση των φυτών γίνεται κυρίως με τη χρήση σπάγκου από νάϋλον γιατί αντέχει στην υγρασία χωρίς προβλήματα, όμως είναι μίας χρήσης. Στύλοι ή καλάμια αποφεύγονται γιατί είναι φορείς ασθενειών και δημιουργούν ευνοϊκές συνθήκες εξάπλωσής τους, μειώνουν τον φωτισμό, έχουν υψηλό κόστος, είναι δυσεύρετα και παρεμποδίζουν την εκτέλεση των καλλιεργητικών εργασιών. Η υποστύλωση αρχίζει 15 - 20 ημέρες μετά τη φύτευση. Το ένα άκρο του σπάγκου στερεώνεται στη βάση του φυτού με χαλαρή θηλιά για να αποφευχθεί το σφίξιμο, ο τραυματισμός και τελικά η αποκοπή του στελέχους με την αύξηση του πάχους του Για να αποφευχθεί ο κίνδυνος αυτός, είναι προτιμότερο ο σπάγκος να δένεται σε σύρμα τεντωμένο κατά μήκος της γραμμής φύτευσης κοντά στο λαιμό των φυτών και στερεωμένο στο έδαφος με διχαλωτά σύρματα. Το άλλο άκρο του σπάγκου δένεται ελαφρά τεντωμένο στο οριζόντιο σύρμα στήριξης των φυτών, που βρίσκεται πάνω από τη γραμμή φύτευσης ή σε ειδικούς μηχανισμούς (γάντζους) τοποθετημένους στο οριζόντιο σύρμα. Τα φυτά τυλίγονται κατά την διάρκεια της ανάπτυξής τους γύρω από τον σπάγκο κατά την φορά των δεικτών του ρολογιού. Όταν γίνεται το τύλιγμα, ο σπάγκος πρέπει να περνά πάνω από την ταξιανθία και όχι κάτω από αυτήν, για να μην υπάρχει κίνδυνος πρόκλησης ζημιάς της κατά την διάρκεια των καλλιεργητικών εργασιών.

Ωρίμανση

Η συγκομιδή του καρπού πρέπει να αρχίζει μετά την έναρξη αλλαγής του χρώματος από το πράσινο στο ελαφρώς κόκκινο. Το ακριβές στάδιο ωριμότητας του καρπού κατά τη συγκομιδή καθορίζεται και από την αγορά προορισμού του προϊόντος. Για παράδειγμα, όταν ο καρπός προορίζεται για την ντόπια αγορά, συγκομίζεται σχεδόν ώριμος.

Συγκομιδή

Η συλλογή των καρπών γίνεται με το χέρι και πρέπει να φέρουν τον κάλυκα και μέρος του ποδίσκου. Είναι προτιμότερο η συγκομιδή να γίνεται τις πρωινές ώρες, όταν η θερμοκρασία είναι χαμηλή και να μεταφέρεται γρήγορα σε δροσερό μέρος για διαλογή και συσκευασία. Για την συγκομιδή χρησιμοποιούνται διάφορα μέσα, όπως πλαστικοί ή μεταλλικοί κουβάδες, πλαστικά, ξύλινα κιβώτια ή χαρτοκιβώτια κ.τ.λ. Καλό θα ήταν η συγκομιδή να γίνεται καθημερινά, αυτό όμως σημαίνει σημαντική επιβάρυνση του κόστους παραγωγής. Για το λόγο αυτό, το χειμώνα η συγκομιδή γίνεται 1 φορά την εβδομάδα, ενώ τις άλλες εποχές του χρόνου γίνεται 2 - 3 φορές την εβδομάδα. Η μέση παραγωγή ενός φυτού ντομάτας που καλλιεργείται στο θερμοκήπιο φτάνει τα 3,5 kg, ενώ η μέση απόδοση της καλλιέργειας ντομάτας υπό κάλυψη ανέρχεται σε 7 - 9 τόνοι /στρέμμα.

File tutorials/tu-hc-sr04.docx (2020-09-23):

Το tutorial, αλλά και η δημιουργία της δεύτερης έκδοσης 3d θήκης αισθητηρα hc-sr04:

Παναγιώτα Τρελλοπούλου

Δημιουργία θήκης hc-sr04

Η θήκη είναι ουσιαστικά το καπάκι ή η βάση για το πίσω μέρος του αισθητήρα υπερήχων hc-sr04. Η χρησιμότητά της, είναι να προστατεύει τον αισθητήρα από την βροχή, καλυπτοντας τον περιμετρικά του σχηματος του. Προκειμένου να σταθεροποιηθεί πάνω στον αισθητήρα, αλλά και στο καπάκι της δεξαμενή, θα δημιουργήσουμε επιπλέον 2 τρύπες, οι οποίες θα έχουν διαστάσεις 2mm, ώστε να μπορέσουμε να το βιδώσουμε.

ΠΡΟΥΠΟΘΕΣΕΙΣ ΓΙΑ ΝΑ ΞΕΚΙΝΗΣΕΤΕ ΤΗΝ ΣΧΕΔΙΑΣΗ ΣΤΟ ΠΡΟΓΡΑΜΜΑ 123D.

1. Η/Υ ή LAPTOP
2. Να έχετε εγκατεστημένο το σχεδιαστικό πρόγραμμα 123d.

Για να εγκαταστήσετε το 123d πρέπει να μεταβείτε στον παρακάτω σύνδεσμο.

https://autodesk-123d-design.en.lo4d.com/download/mirror-ex2

3. Να έχετε κάποιες βασικές γνώσεις για το πρόγραμμα(Αν όχι πρέπει να δείτε το βίντεο πιο πάνω στην ιστοσελίδα).
4. Για να μπορέσετε να το εκτυπώσετε την θήκη είναι απαραίτητη η κατοχή 3d εκτυπωτή και κατά προτίμηση σαν filament να είναι PLA.

Προτού αρχίσουμε την περιγραφή του πώς φτιάξαμε τι, ώστε να μπορέσετε να το φτιάξετε και εσείς, θα σας παρακαλούσαμε να παρακολουθήσετε επιπλέον και το παρακάτω βίντεο που φτιάξαμε. Αυτό, διότι θα γίνει μια σύντομη, αλλά περιεκτική περιγραφή, όσον αφορά την διαδικασία που ακολούθησε, προκειμένου να φτάσουμε στο τελικό αποτέλεσμα της 3d θήκης του αισθητηρα hc-sr04.

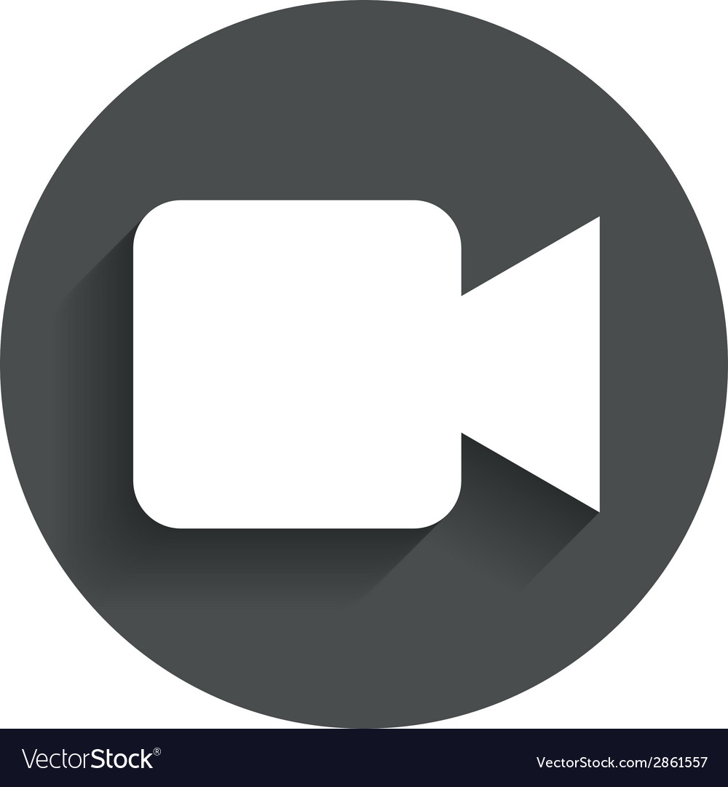
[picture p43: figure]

## (https://www.youtube.com/watch?v=ng9dO-1iB60&t=80s)

ΒΗΜΑ 1: Το πρώτο βήμα που θα πρέπει να ακολουθήσετε,είναι να πάτε στο 123d. Αφού το κάνετε αυτό, θα πρέπει να πάτε στην λειτουργία sketch και να επιλέξετε το πρώτο υπο εικονίδιο που σας παρουσιάζεται σαν επιλογή με το σχήμα ορθογώνιου και με την ονομασία sketch rectangle, όπως βλέπετε και παρακάτω στην εικόνα 1.

Εικόνα 1:Η μπάρα επιλογών του sketch. Επίσης, στο κόκκινο πλαίσιο βρίσκεται η λειτουργία sketch rectangle, που πρέπει να επιλέξετε.

Αφού, επιλέξετε ένα σημείο πάνω στο workplane με αριστερό κλικ στο ποντίκι, αμέσως μετά σύρετε το ποντίκι βλέποντας να αναπτύσσεται ένα τετράγωνο. Έπειτα, πληκτρολογήστε μέσα στα πλαίσια τις διαστάσεις 21mm x 46mm και πατήστε κλικ για ολοκλήρωση του σχήματος , όπως φαίνεται και στην εικόνα 2.

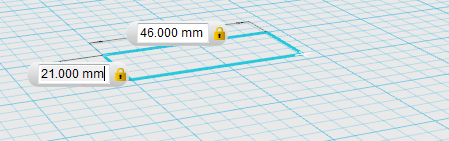
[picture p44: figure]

Εικόνα 2: Το 2d sketch που πρέπει να σχεδιάσετε.

Έπειτα, επιλέγοντας ξανά την λειτουργία sketch, θα πάτε πάλι στα υπο εικονίδια και θα επιλέξετε το προτελευταίο από αυτά, δηλαδή αυτό που λέει offset, όπως και στην εικόνα 3.

Εικόνα 3:Η μπάρα επιλογών του sketch. Στο κόκκινο πλαίσιο βρίσκεται η επιλογή offset.

Ύστερα, θα επιλέξετε μία από τις περιμετρικές γραμμές στο 2d sketch που σχεδιάσατε πριν λίγο. Σύροντας το ποντίκι θα δείτε πως αναδεικνύεται ένα καινούριο 2d sketch(ορθογώνιο), το οποίο βρίσκεται σε κόκκινο πλαίσιο. Επίσης, θα διαπιστώσετε πως σας δίνει και ένα κουτάκι για να γράψετε αριθμούς. Εκεί λοιπόν, θα πατήσετε τον αριθμό 2 και θα δείτε πως θα σχεδιάστηκε και ένα δεύτερο 2d sketch, 2mm μεγαλύτερο από το πρώτο σε όλη την περίμετρο. Η εικόνα 4 θα σας δείξει το πώς πρέπει να μοιάζει όταν τελειώσετε.

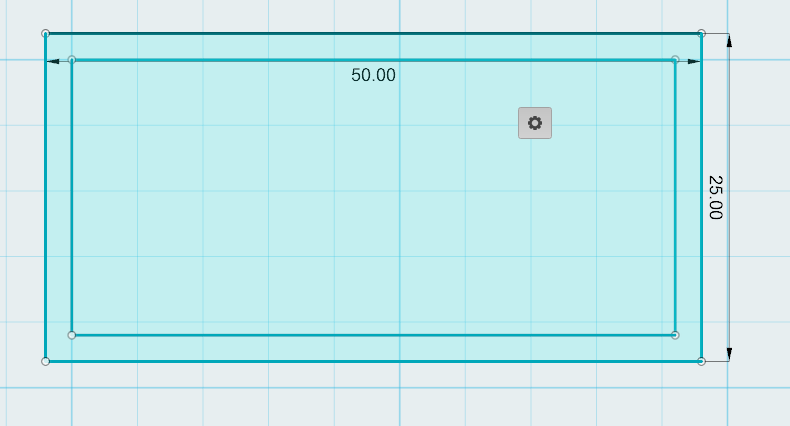
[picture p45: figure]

Εικόνα 4: Η τελική μορφή των 2d sketch .

Αφού κάνετε αυτά, σειρά έχει να μετατρέψετε τα 2d sketches σε 3d. Για να το κάνετε αυτό, θα πρέπει να επιλέξετε ένα-ένα το κάθε 2d sketch και να επιλέξετε την λειτουργία extrude, δηλαδή την τρίτη από τις επιλογές που θα σας δώσει το πρόγραμμα αφού φυσικά έχετε επιλέξει προηγουμένως το γρανάζι που εμφανίζεται, κάθε φορά που επιλέγετε κάποιο αντικείμενο, όπως φαίνεται και στην εικόνα 5. Μετά, θα σας εμφανίσει και ένα βελάκι πάνω στο 2d sketch. Καλό θα ήταν να μην τραβήξετε το βελάκι και να πατήσετε απλά τον αριθμό 2 στο πρώτο sketch που κάναμε και 7 στο δεύτερο. Οι αριθμοί 2 και 7, σημαίνει πως το πρώτο sketch θα έχει ύψος 2mm και το άλλο sketch θα έχει ύψος 7mm.

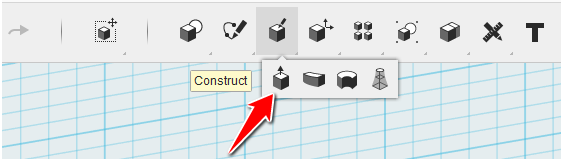
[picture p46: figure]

`

Εικόνα 5: Το κόκκινο βέλος δείχνει το εικονίδιο του extrude.

Αν τελειώσετε με αυτό, θα δείτε ότι έχετε σχηματίσει τον χώρο που θα τοποθετηθεί ο αισθητήρας,όπως φαίνεται και στην εικόνα 6.

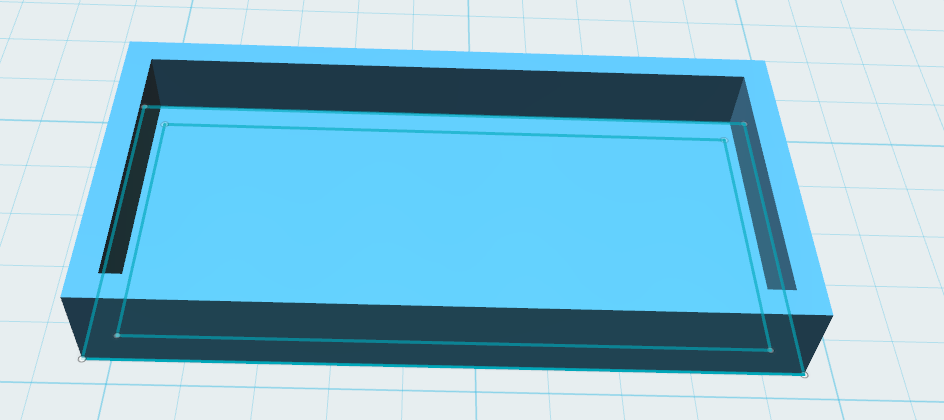
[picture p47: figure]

Εικόνα 6: Η 3d ,πλέον, θήκη του αισθητήρα μετά την διαδικασία extrude.

Τελευταίο βήμα για να ολοκληρώσουμε την 3d σχεδίαση της βάσης της θήκης του αισθητηρα hc-sr04, είναι να στρογγυλέψουμε τις 4 γωνίες της βάσης. Για να το κάνουμε λοιπόν αυτό, θα πρέπει να επιλέξουμε τις ακμές ανά ζεύγος, προκειμένου να γίνουν ομοιόμορφες. Οπότε, για να επιλέξετε και τις 2 γωνίες μαζί, πατάτε αριστερό κλικ στο ποντίκι πάνω στο αντικείμενο και θα δείτε πως αν επιχειρήσετε να πατήσετε κάπου πάνω στο αντικείμενο για δεύτερη φορά, θα έχετε την δυνατότητα να επιλέξετε πλευρές, γωνίες, ακμές κ.λ.π. Πατάτε λοιπόν στην πρώτη κάθετη ακμή shift στο πληκτρολόγιο και μετά επιλέγετε και την δεύτερη. Τότε, πατάτε το γρανάζι που θα εμφανιστεί και επιλέγετε την υπο επιλογή fillet. Καλό θα ήταν να μην τραβήξετε το βελάκι και να πατήσετε απλά τον αριθμό 2. Το αποτέλεσμα θα πρέπει να είναι το παρακάτω, όπως και στις εικόνες 7 και 8.

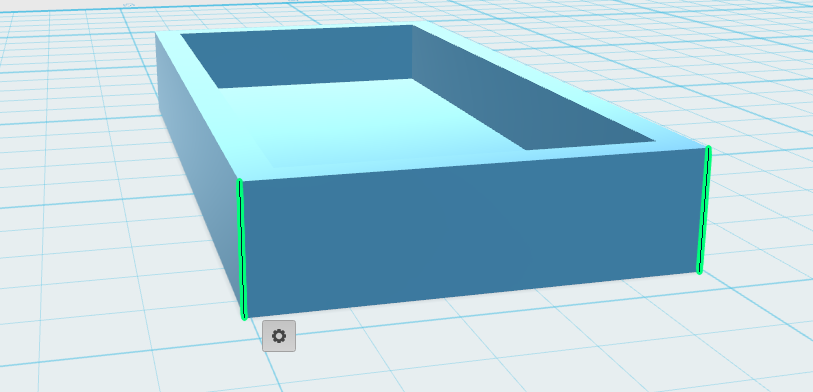
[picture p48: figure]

Εικόνα 7: Οι 2 επιλεγμένες γωνίες, καθώς και το γρανάζι που εμφανίζεται όταν τις επιλέγετε.

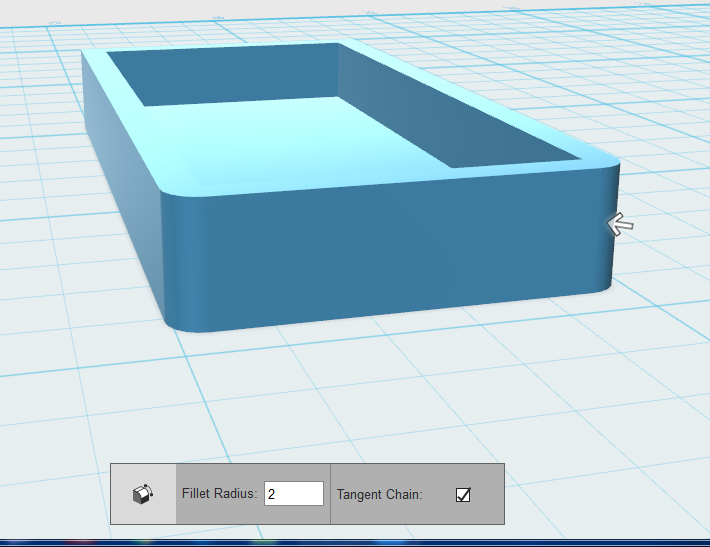
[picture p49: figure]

Εικόνα 8: Εδώ βλέπετε, τις 2 στρογγυλεμένες γωνίες που προέκυψαν από την παραπάνω διαδικασία.

ΒΗΜΑ 2: Αφού τελειώσαμε με την σχεδίαση της βάσης για την θήκη, σειρά έχει η σχεδίαση ενός ανοίγματος στην μια πλευρά του αντικειμένου στο κάτω μέρος της βάσης της θήκης. Αυτό το ορθογώνιο άνοιγμα θα έχει ως σκοπό να μπορούν να προεξέχουν ανενόχλητοι οι ακροδέκτες του αισθητήρα.

Το πρώτο που θα πρέπει να κάνετε, προκειμένου να δημιουργήσουμε το άνοιγμα για τους ακροδέκτες, είναι να πάτε στην κεντρική μπάρα εργαλείων στα primitives και από τις υπο επιλογές που υπάρχουν, να διαλέξετε 2 από το πρώτο σχήμα, τον απλό κύβο και έναν κύλινδρο, όπως φαίνεται και στην εικόνα 9.

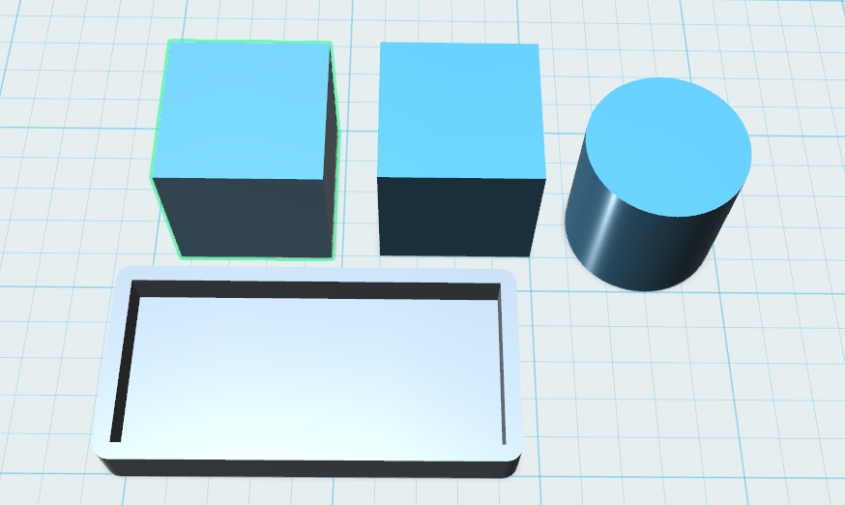
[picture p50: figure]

Εικόνα 9: Οι 2 κύβους και τον 1 κύλινδρο από την τα primitives.

Μετά, επιλέξτε με αριστερό κλικ στο ποντίκι έναν από τους κύβους και στις υπο επιλογές που θα σας εμφανιστούν, διαλέξτε το δεύτερο εικονίδιο με την ονομασία Smart Scale. Αφού γίνει αυτό, θα παρατηρήσετε πως σας δίνει τις διαστάσεις του αντικειμένου. Επιλέξτε μία πλευρά και τώρα αλλάξτε τις διαστάσεις από 20mm σε 10mm. Αφού λοιπόν το κάνετε αυτό, μεταφέρεται τον τροποποιημένο κύβο στο κάτω μέρος της βάσης που σχεδιάσαμε πριν από λίγο, όπως φαίνεται και στην εικόνα 10.

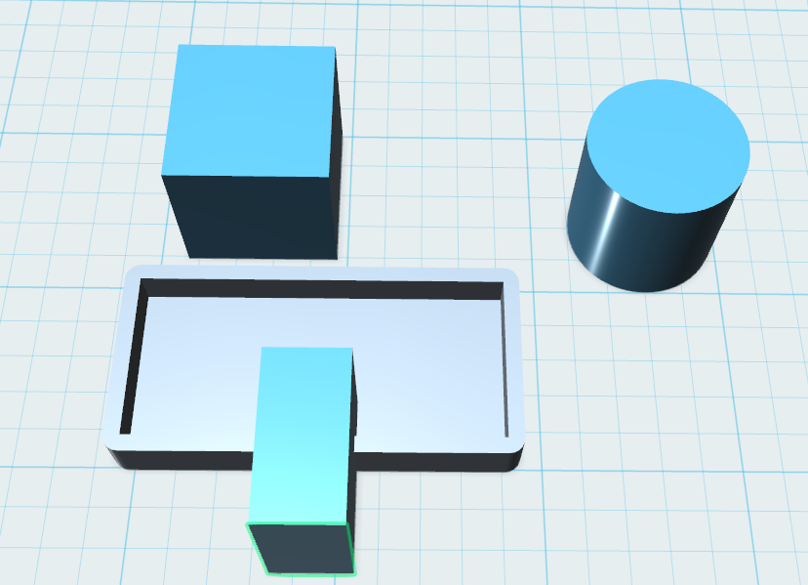
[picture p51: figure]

Εικόνα 10: Η μεταφορά του κύβου στο κάτω μέρος της βάσης.

Αφού λοιπόν το μετακινήσετε εκεί, προκειμένου να το ευθυγραμμίσετε με την βάση, θα πρέπει να χρησιμοποιήσετε την λειτουργία align, η οποία

βρίσκεται σαν υπο εικονίδιο της μπάρας εργαλείων transform πάνω αριστερά στο μέρους του χώρου εργασίας σας. Θα χρειαστεί να πατήσουμε μόνο την κεντρική κουκίδα στο κάτω μέρος από αυτές που θα μας εμφανιστούν.

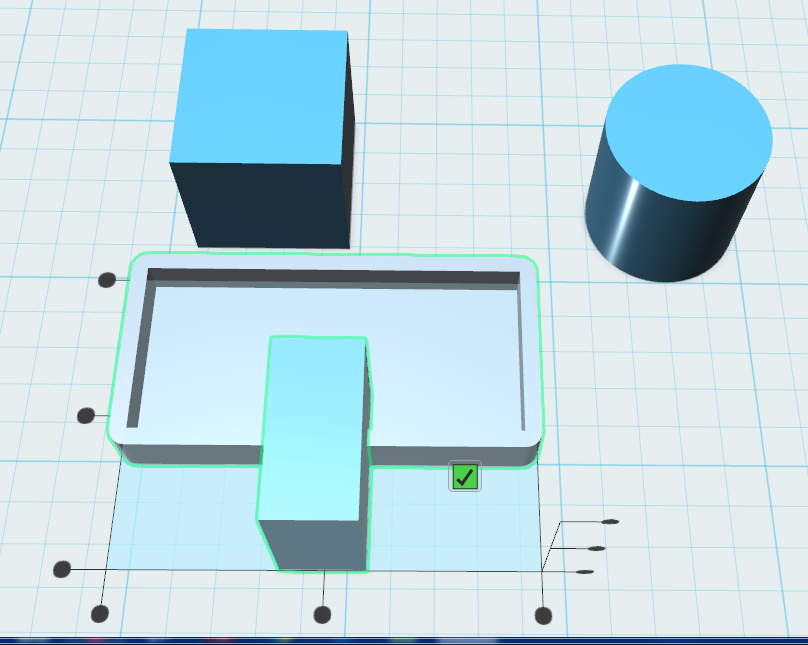
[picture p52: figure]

Εικόνα 11:Η λειτουργία align, για να φέρουμε το αντικείμενο στο κέντρο.

Έπειτα, προκειμένου να μπορέσουμε να μετατρέψουμε το ορθογώνιο παραλληλεπίπεδο σε τρύπα, ώστε να δημιουργηθεί το άνοιγμα πάνω στην βάση, θα πρέπει να πάτε στην λειτουργία combine και να επιλέξετε την υπο λειτουργία subtract. Αμέσως μετά, πρέπει να επιλέξετε την βάση και αφού πατήσετε το shift στο πληκτρολόγιο, επιλέξτε και το ορθογώνιο παραλληλεπίπεδο. Τότε, θα δείτε ότι έχει δημιουργηθεί ένα ορθογώνιο άνοιγμα στο κάτω μέρος της βάσης, όπως φαίνεται και στην εικόνα 12.

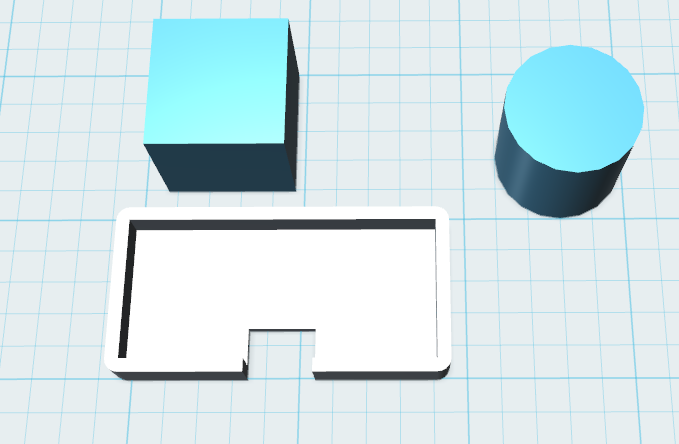
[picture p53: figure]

Εικόνα 12:Το άνοιγμα που σχηματίστηκε στην βάση της θήκης.

ΒΗΜΑ 3: Τελευταίο βήμα για την σχεδίαση της θήκης του αισθητηρα hc-sr04, είναι να δημιουργήσουμε 2 ίδια αντικείμενα, τα οποία θα λειτουργήσουν σαν στηρίγματα, καθώς θα βιδώσουν την θήκη πάνω στο καπάκι της δεξαμενής.

Αρχικά λοιπόν, προκειμένου να σχεδιάσουμε τα <<αυτιά>> αυτά, θα πρέπει να αλλάξουμε τις διαστάσεις του κυλίνδρου από 20mm σε 2mm, όπως φαίνεται και στην εικόνα 13.

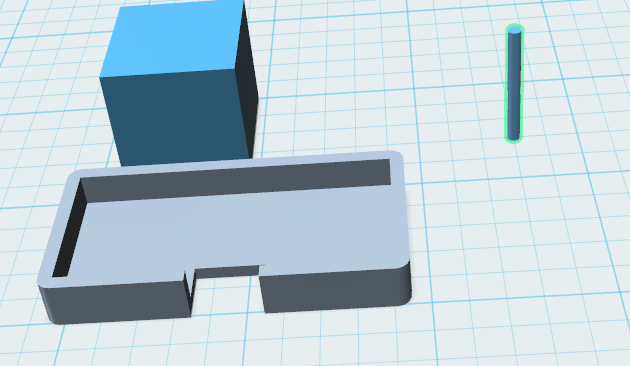
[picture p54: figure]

Εικόνα 13: Ο τροποποιημένος κύλινδρος.

Επόμενο βήμα, είναι να αλλάξετε τις διαστάσεις του κύβου από 20χ20mm σε 8χ7 mm και το ύψος του 2mm. Η εικόνα 14 δείχνει την μορφή που πρέπει να έχει ο κύβος όταν εκτελέσετε τις παραπάνω εντολές.

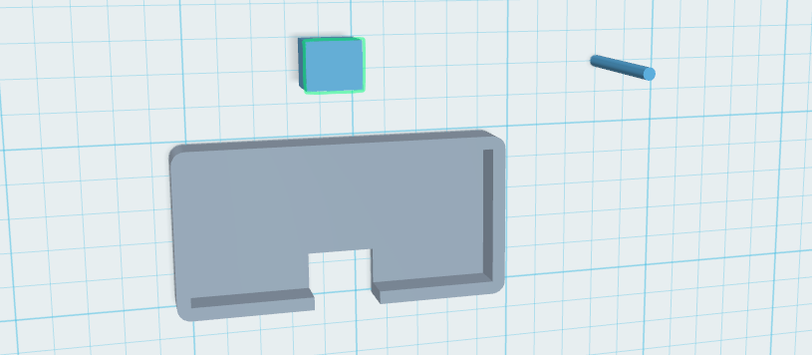
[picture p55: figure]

Εικόνα 14: Ο τροποποιημένος κύβος.

Αφού λοιπόν φτιάξετε το ορθογώνιο αυτό, μετά στρογγυλοποιήστε τις 2 μόνο κάθετες ακμές κατά 3mm, όπως ακριβώς φαίνεται και στην εικόνα 14.

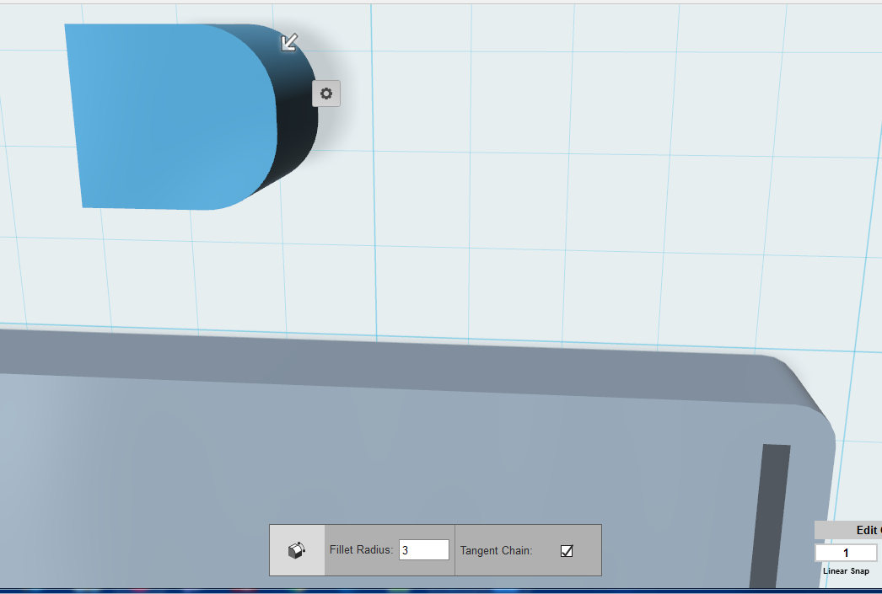
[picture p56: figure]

Εικόνα 15: Οι στρογγυλεμένες γωνίες του ορθογωνίου.

Ύστερα, μεταφέρετε τον κύλινδρο μέσα στο λεγόμενο <<αυτί>> που σχεδιάσαμε πριν από λίγο και κάντε align χρησιμοποιώντας όλες τις μεσαίες κουκίδες που θα σας παρουσιαστούν, με εξαίρεση αυτή του ύψους. Όπως δείχνει η εικόνα 16 για να ευθυγραμμιστεί ο κύλινδρος μέσα στο λεγόμενο αυτί.

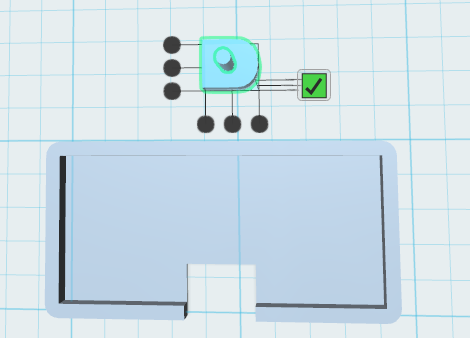
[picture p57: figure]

Εικόνα 16: Η ευθυγράμμιση του κυλίνδρου.

Μετά από αυτό, θα πρέπει να επαναλάβετε την διαδικασία μετατροπής του κυλίνδρου σε τρύπα. Αυτό, όπως καταλαβαίνετε, σημαίνει πως πρέπει να πάτε στην μπάρα λειτουργίας combine και να επιλέξετε το υπο εικονίδιο, που ονομάζεται subtract, αφού πρώτα έχετε επιλέξει αρχικά το <<αυτί>> και μετά πατώντας shift και τον κύλινδρο. Το τελικό αποτέλεσμα, θα πρέπει να είναι ίδιο με την εικόνα 17.

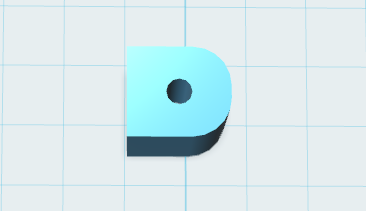
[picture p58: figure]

Εικόνα 17:Η τρύπα που σχηματίστηκε.

Για να γλυτώσουμε την επανάληψη όλης αυτής της διαδικασίας, προκειμένου να σχεδιάσουμε και το δεύτερο <<αυτί>>, θα επιλέξουμε το <<αυτί>> που μόλις σχεδιάσαμε και θα πατήσουμε στο πληκτρολόγιο control και c και μετά πατήστε control και v. Τότε θα παρατηρήσετε ότι εμφανίστηκε ένα ολόιδιο <<αυτί>>με αυτό που μόλις σχεδιάσαμε. Τώρα για να τα ενώσουμε με την βάση της θήκης, θα πρέπει να επιλέξουμε την λεία επιφάνεια (δηλαδή της επιφάνειας απέναντι από αυτή με την στρογγυλή επιφάνεια) του ενός από τα δύο <<αυτιά>> που σχεδιάσαμε και μετά αφού επιλέξουμε την λειτουργία snap επιλέγουμε μια από τις δύο πλαϊνές πλευρές της βάσης, όπως και στην εικόνα 18. Επαναλάβετε αυτήν την διαδικασία και με το άλλο <<αυτί>>. Αν το κάνατε αυτό, θα πρέπει να έχετε το αποτέλεσμα που φαίνεται και στην εικόνα 19.

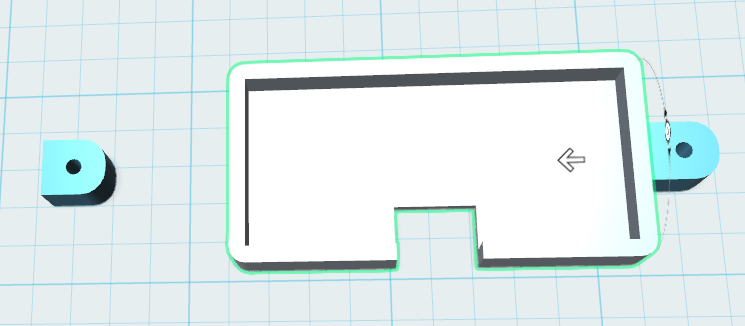
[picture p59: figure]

Εικόνα 18: Η ένωση των <<αυτιών>> με την βάση της θήκης.

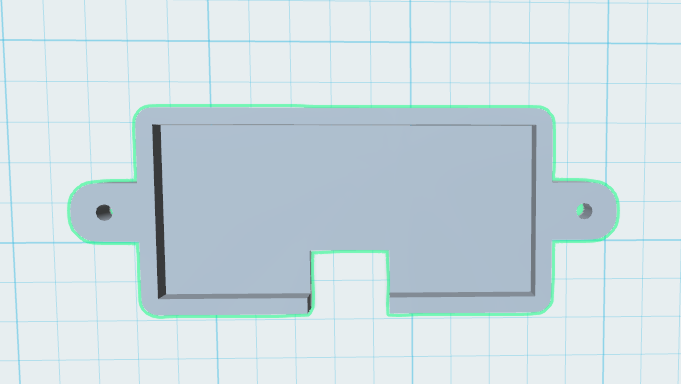
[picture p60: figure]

Εικόνα 19: Η τελική μορφή της 3d θήκης του αισθητήρα hc-sr04. Αν ακολουθήσατε σωστά τα παραπάνω βήματα, τότε αυτό θα είναι και το τελικό αποτέλεσμα.

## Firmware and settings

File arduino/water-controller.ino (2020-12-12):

//step motor
const int enablePin = 36;
const int m0pin = 38;
const int m1pin = 40;
const int m2pin =42;
const int endstop = 14;
const int dirPin = 15;
const int stepPin = 16;
const int stepsPerRevolution = 200;
const int axisStep = 1300;
int stepdelay = 500;
//hw-103
const int analogHw = A8; 
int soilMoisture;
int buf4[10];
int avgValue4;
int v;
//PH
const int analogInPin = A15; 
int sensorValue = 0; 
unsigned long int avgValue; 
float b;
int buf[10],temp;
float phValue;

//HC-SR04
int x;
int y;
int z;
unsigned long int avgValue1;
unsigned long int avgValue2;
unsigned long int avgValue3;
int buf1[10];
int buf2[10];
int buf3[10];
const int echoPin1 =23;
const int trigPin1 =22;
long duration1;
int distance1;
const int echoPin2 =34;
const int trigPin2 =35;
long duration2;
int distance2;
const int echoPin3 = 20;
const int trigPin3 =19;
long duration3;
int distance3;
int tankfill1; //pososto stathmis neroy tank clear
int tankfill2;
int tankfill3;
int delayHcsr = 10;
//water lever sensor analog input
int level_input=21; // analog input
//Relay
int Relay1 =45 ;// hlektrobana k
int Relay2 =46 ;// hlektrobana o
int Relay3 =47 ;// potisma
int Relay4 =48 ;// antlia k
int Relay5 =49 ;// keno
int Relay6 =50 ;// antlia e
int Relay7 =51;
int Relay8 =52;
int a = 0;
int g = 0;
int c = 0;
int d = 0;
int e = 0;
int f = 0;
//led
int led1 =25 ;
int led2 =24 ;
int led3 =26 ;
int led4 =28 ;
int led5 =30 ;
int led6 =32 ;
//switch
int switch1 =A9;
int switch2 =A10;
int switch3 =A11;
int switch4 =A12;
int switch5 =A13;
int switch6 =A14;
#include <LiquidCrystal.h>
//LCD pin to Arduino
const int pin_RS = 8; 
const int pin_EN = 9; 
const int pin_d4 = 4; 
const int pin_d5 = 5; 
const int pin_d6 = 6; 
const int pin_d7 = 7; 
const int pin_BL = 10; 
LiquidCrystal lcd( pin_RS,  pin_EN,  pin_d4,  pin_d5,  pin_d6,  pin_d7);
const int lcd_buttons = A0;
int l;
int delayDisplay = 500;
unsigned long time1;
void setup() {
     
  // put your setup code here, to run once:
 Serial.begin(9600);
 //lcd
 pinMode(lcd_buttons, INPUT); //A0
 lcd.begin(16, 2);
 lcd.setCursor(0,0);
 lcd.print("Process:");
 lcd.setCursor(0,1);
 lcd.print("Initialazition");
 delay(delayDisplay);
 lcd.setCursor(0,1);
 lcd.print("                 ");
 //STEP MOTOR
  pinMode(enablePin,OUTPUT);
  pinMode(m0pin,OUTPUT);
  pinMode(m1pin,OUTPUT);
  pinMode(m2pin,OUTPUT);
  pinMode(stepPin, OUTPUT);
  pinMode(dirPin, OUTPUT);
  pinMode(endstop,INPUT);
  digitalWrite(enablePin,HIGH);
   
  lcd.setCursor(9,0);
 lcd.print("Step Motor");
 stepperhome();
 
 lcd.clear();
 lcd.print("Process:");
 lcd.setCursor(9,0);
 lcd.print("               ");
 //Relay
 
 pinMode(Relay1 , OUTPUT );
 pinMode(Relay2 , OUTPUT );
 pinMode(Relay3 , OUTPUT );
 pinMode(Relay4 , OUTPUT );
 pinMode(Relay5 , OUTPUT );
 pinMode(Relay6 , OUTPUT );
 pinMode(Relay7 , OUTPUT );
 pinMode(Relay8 , OUTPUT );

 digitalWrite(Relay1 , HIGH);
 digitalWrite(Relay2 , HIGH);
 digitalWrite(Relay3 , HIGH);
 digitalWrite(Relay4 , HIGH);
 digitalWrite(Relay5 , HIGH);
 digitalWrite(Relay6 , HIGH);
 digitalWrite(Relay7 , HIGH);
 digitalWrite(Relay8 , HIGH);
 delay(1000);
 
 

  


//ph
 
pinMode(A15 , INPUT );
lcd.setCursor(9,0);
lcd.print("Ph");
delay(delayDisplay);

 ph();
 if ((phValue >= 0) && (phValue <= 14)){
 lcd.setCursor(0,1);
 lcd.print("Test ok");
 delay(delayDisplay);
 }
 else{
 lcd.setCursor(0,1);
 lcd.print("Test fail");
 delay(delayDisplay);
 }
 lcd.setCursor(9,0);
 lcd.print("                 ");
 lcd.setCursor(0,1);
 lcd.print("                 ");

//hcsr1 test
 lcd.setCursor(9,0);
 lcd.print(" Hcsr-C");
 delay(delayDisplay);

pinMode(trigPin1 , OUTPUT );
pinMode(echoPin1 , INPUT );
hcsr1();
if ( (tankfill1 >= 0) && (tankfill1 <=100) ){
 lcd.setCursor(0,1);
 lcd.print("Test ok");
 delay(delayDisplay);
}
else{
 lcd.setCursor(0,1);
 lcd.print("Test Fail");
 delay(delayDisplay);
}
 lcd.setCursor(9,0);
 lcd.print("                 ");
 lcd.setCursor(0,1);
 lcd.print("                 ");
//hcsr2
 lcd.setCursor(9,0);
 lcd.print("Hcsr-O");
 delay(delayDisplay);
 
pinMode(trigPin2 , OUTPUT );
pinMode(echoPin2 , INPUT );
hcsr2();
if ( (tankfill2 >= 0) && (tankfill2 <=100)){
lcd.setCursor(0,1);
lcd.print("Test ok");
delay(delayDisplay);
lcd.setCursor(0,1);
lcd.print("                 ");
}
else{
lcd.setCursor(0,1);
lcd.print("Test Fail");
delay(delayDisplay);
}
 lcd.setCursor(9,0);
 lcd.print("                 ");
 lcd.setCursor(0,1);
 lcd.print("                 ");

//hcsr3
 lcd.setCursor(9,0);
 lcd.print("Hcsr-E");
 delay(delayDisplay);
 
pinMode(trigPin3 , OUTPUT );
pinMode(echoPin3 , INPUT );
hcsr3();
if ( (tankfill3 >= 0) && (tankfill3 <=100)){
  lcd.setCursor(0,1);
  lcd.print("Test ok");
  delay(delayDisplay);
  lcd.setCursor(0,1);
  lcd.print("                 ");
}
else{
  lcd.setCursor(0,1);
  lcd.print("Test Fail");
  delay(delayDisplay);
}
 lcd.setCursor(9,0);
 lcd.print("                 ");
 lcd.setCursor(0,1);
 lcd.print("                 ");

// water level
 lcd.setCursor(8,0);
 lcd.print("Waterlevel");
 delay(delayDisplay);
 
pinMode(level_input , INPUT);
if(digitalRead(level_input) == LOW){
   lcd.setCursor(0,1);
   lcd.print("State:Close");
   delay(delayDisplay);
}
else{
  lcd.setCursor(0,1);
  lcd.print("State:Open");
  delay(delayDisplay);
}
  lcd.setCursor(8,0);
  lcd.print("                 ");
  lcd.setCursor(0,1);
  lcd.print("                 ");

//switch
  lcd.setCursor(8,0);
  lcd.print("Switches");
  delay(delayDisplay);
  pinMode(switch1 , INPUT);
  pinMode(switch2 , INPUT);
  pinMode(switch3 , INPUT);
  pinMode(switch4 , INPUT);
  pinMode(switch5 , INPUT);
  pinMode(switch6 , INPUT);

if ((analogRead(switch1) > 800) && (analogRead(switch2) > 800) && (analogRead(switch3) > 800) && (analogRead(switch4) > 800) && (analogRead(switch5) > 800) && (analogRead(switch6) > 800)) {
   lcd.setCursor(0,1);
   lcd.print("Test ok");
   delay(delayDisplay);
}
else{
  lcd.setCursor(0,1);
  lcd.print("Test fail");
  delay(delayDisplay);
}
  lcd.setCursor(8,0);
  lcd.print("                 ");
  lcd.setCursor(0,1);
  lcd.print("                 ");

//led
  lcd.setCursor(0,1);
  lcd.print("Leds");
  delay(delayDisplay);
  lcd.setCursor(0,1);
  lcd.print("                 ");
  pinMode(led1 , INPUT);
  pinMode(led2 , INPUT);
  pinMode(led3 , INPUT);
  pinMode(led4 , INPUT);
  pinMode(led5 , INPUT);
  pinMode(led6 , INPUT);
 
digitalWrite(led1 , HIGH);
digitalWrite(led2 , HIGH);
digitalWrite(led3 , HIGH);
digitalWrite(led4 , HIGH);
digitalWrite(led5 , HIGH);
digitalWrite(led6 , HIGH);
delay(1000);

digitalWrite(led1 , LOW);
digitalWrite(led2 , LOW);
digitalWrite(led3 , LOW);
digitalWrite(led4 , LOW);
digitalWrite(led5 , LOW);
digitalWrite(led6 , LOW);
delay(1000);

//hw103
  lcd.setCursor(8,0);
  lcd.print("Hw-103");
  delay(delayDisplay);
  pinMode(analogHw,INPUT);

hw103();
if((soilMoisture >= 0) && (soilMoisture <= 100)){
  lcd.setCursor(0,1);
  lcd.print("Test ok");
  delay(delayDisplay);
}
else{
    lcd.setCursor(0,1);
    lcd.print("Test fail");
    delay(delayDisplay);
}
  lcd.setCursor(8,0);
  lcd.print("                 ");
  lcd.setCursor(0,1);
  lcd.print("                 ");


//init done
  lcd.setCursor(0,1);
  lcd.print("Init done");
  delay(delayDisplay);
  //lcd.noDisplay()();
  lcd.clear();
  lcd.print("Real Inventors");
  Serial.println("ready");
  time1 = millis();
  }//end setup

///////////////////////////////////////////////////////////////////////////////////////////////////////////////////////////////////////////////////////////////////////////////////////////////////
void loop() {
  
if (millis() - time1 > 15000){
    Serial.println(millis());
   Serial.println(time1);
    Serial.println(millis()-time1);
  lcd.noDisplay();
  time1 = millis();

}
 
  // put your main code here, to run repeatedly:
 hcsr1(); //function level tank 1 (clean) tankfill1
 hcsr2(); //function level tank 2 (ojino) tankfill2
 hcsr3(); //function level tank 3 (elegxoy) tankfill3
 


  //water lever sensor analog input  
 if(digitalRead(level_input) == LOW){// check water level
   ph(); // function ph phValue
 if(phValue >= 6,9) {// check ph
  if((tankfill1 <= 70) && (tankfill3 >= 35)){
    digitalWrite(Relay1 , LOW);
  digitalWrite(led1 , HIGH);
  delay(500);
  digitalWrite(Relay4 , LOW);
  lcd.display();
  lcd.clear();
  lcd.print("Please wait");
  while((tankfill1 <= 70) && (tankfill3 >= 35)){
  hcsr1();
  hcsr3();
  // delay(delayDisplay);
 }
  digitalWrite(Relay1 , HIGH);
  digitalWrite(led1 , LOW);
  delay(500);
  digitalWrite(Relay4 , HIGH);
  //lcd.noDisplay()();
  }//end fill tankc



 }//end if ph +7,2


 
 if(phValue < 6,9) {// check ph
if((tankfill2 <= 70) && (tankfill3 >= 35)){
 digitalWrite(Relay2,LOW);
 digitalWrite(led2,HIGH);
   }//end fill tanko
 else{
  digitalWrite(Relay2,HIGH);
  digitalWrite(led2,LOW);
  delay(500);
 }
 }//end if ph -7,2
 }// end if switch low
else{//water level open
 if(digitalRead(Relay2) == LOW){
 if ((tankfill2 >= 70) || (tankfill3 <= 35)){
   digitalWrite(Relay2,HIGH);
   digitalWrite(led2,LOW);
  }
 }

 }//end else
 
hw103(); //function plant soilmoisture
 if((soilMoisture <= 30) && (tankfill1 >= 45)){//potisma
    digitalWrite(Relay3,LOW);
    digitalWrite(led3,HIGH);
    delay(500);
    digitalWrite(Relay5 , LOW);
      lcd.display();
  lcd.clear();
  lcd.print("Please wait");
    stepperhome();
  while((soilMoisture <= 50) && (tankfill1 >= 45)){
    hw103();
    hcsr1();
   steppermotor();    
}
 digitalWrite(enablePin,HIGH);
   //klisimo potisma
   //lcd.noDisplay()();
 digitalWrite(Relay3,HIGH);
    digitalWrite(led3,LOW);
    digitalWrite(Relay5 ,HIGH); 
 }

    
  




//anoigma fill clean
if( analogRead(switch1) < 200) {
  lcd.display();
  lcd.clear();
  lcd.setCursor(0,0);
  lcd.print("Switch1 close");
  lcd.setCursor(0,1);
  lcd.print("Fill Tank-C");
  //delayDisplay;
  digitalWrite(Relay1 , LOW);// anoije hlektrobana, antlia
  digitalWrite(led1 , HIGH); 
  delay(500);
  digitalWrite(Relay4 , LOW);
 

while(( analogRead(switch1) < 200)&&(tankfill1 <=80)&&(tankfill3>=35)) {
hcsr1();
hcsr3();


}
  //lcd.noDisplay()();
  digitalWrite(Relay1,HIGH);
     digitalWrite(led1,LOW);
     digitalWrite(Relay4,HIGH);
}
// tank o fill

if( analogRead(switch2) < 200) {
  lcd.display();
  lcd.clear();
  lcd.setCursor(0,0);
  lcd.print("Switch2 close");
  lcd.setCursor(0,1);
  lcd.print("Fill Tank-O");
  //delay(delayDisplay);
  digitalWrite(Relay2 , LOW);
  digitalWrite(led2 , HIGH); 

while(( analogRead(switch1) < 200)&&(tankfill2 <=80)&&(tankfill3>=35)) {
hcsr2();
hcsr3();


}
  //lcd.noDisplay()();
   digitalWrite(Relay2,HIGH);
   digitalWrite(led2,LOW);
}



//potisma



if( analogRead(switch3) < 200) {
     lcd.display();
   lcd.clear();
  lcd.setCursor(0,0);
  lcd.print("Switch3 close");
  lcd.setCursor(0,1);
  lcd.print("Water Plants");
  //delay(delayDisplay);
  stepperhome();
  digitalWrite(Relay3, LOW);
  digitalWrite(led3 , HIGH); 
  delay(500);
  digitalWrite(Relay5 , LOW);
  


while(( analogRead(switch3) < 200)&&(tankfill1>=35)) {

 
steppermotor();
hcsr1();
}
 digitalWrite(enablePin,HIGH);
  //lcd.noDisplay()();
digitalWrite(Relay3,HIGH);
     digitalWrite(led3,LOW);
     
     digitalWrite(Relay5 , HIGH);
}
  
 
//fill tank e 
if( analogRead(switch4) < 200) {
    lcd.display();
  lcd.clear();
  lcd.setCursor(0,0);
  lcd.print("Switch4 close");
  //delay(delayDisplay);
digitalWrite(Relay8 , LOW);
  digitalWrite(led4 , HIGH); 

  delay(500);
    digitalWrite(Relay7 , LOW);
 while((analogRead(switch4) < 200) && (tankfill3 <= 80)){
  hcsr3();
}
  //lcd.noDisplay()();
digitalWrite(Relay8 , HIGH);
  digitalWrite(led4 , LOW);
  delay(500);
    digitalWrite(Relay7 ,HIGH);
 }
//test stepper
if( analogRead(switch5) < 200) {
    lcd.display();
  lcd.clear();
  lcd.setCursor(0,0);
  lcd.print("Switch5 close");
  lcd.setCursor(0,1);
  lcd.print("Stepper");
  //delay(delayDisplay);
  stepperhome();
while(analogRead(switch5) < 200){
  steppermotor();
}
  //lcd.noDisplay()();
 digitalWrite(enablePin,HIGH);
}


//fota spiti

if(( analogRead(switch6) < 200)&&( c==0)) {
    lcd.display();
  lcd.clear();
  lcd.setCursor(0,0);
  lcd.print("Switch6 close");
    lcd.setCursor(0,1);
  lcd.print("House Lights");
  //delay(delayDisplay);
  digitalWrite(Relay6 , LOW);
  digitalWrite(led6 , HIGH);
    digitalWrite(Relay3 , LOW);
//lcd.noDisplay()();

c =1;


}

if( analogRead(switch6) > 200) {
digitalWrite(Relay6 , HIGH);
 digitalWrite(led6 , LOW);
 digitalWrite(Relay3 ,HIGH );

c =0;
}

//D1 Robot
int x;
x = analogRead(lcd_buttons);
lcd.setCursor(10,1);
if (x < 60) {
  //hcsr
  //right
  lcd.display();
  lcd.clear();
  lcd.setCursor(0,0);
  lcd.print("Tank-C:");
  lcd.setCursor(7,0);
  lcd.print(tankfill1);
  lcd.setCursor(10,0);
  lcd.print("%");

  lcd.setCursor(0,1);
  lcd.print("Tank-O:");
  lcd.setCursor(7,1);
  lcd.print(tankfill2);
  lcd.setCursor(10,1);
  lcd.print("%");
  //delay(delayDisplay);

time1 = millis();
  //delay(delayDisplay);
//lcd.noDisplay()();
}
else if (x < 200) {
 //water level
//UP
lcd.display();
  lcd.clear();
   lcd.print("Water Level");
   //delay(delayDisplay);
    if(digitalRead(level_input) == LOW){// check water level
   lcd.setCursor(0,1);
   lcd.print("State:Closed");
   //delay(delayDisplay);
    }
    else{
      lcd.setCursor(0,1);
   lcd.print("State:Open");
   //delay(delayDisplay); 
    }
    time1 = millis();
    //lcd.noDisplay()();
}
else if (x < 400){
   //ph
   //down
   lcd.display();
   lcd.clear();
   ph(); // function ph phValue
   lcd.setCursor(0,1);
   lcd.print("ph:");
   lcd.setCursor(4  ,1);
   lcd.print(phValue);
   //delay(delayDisplay);
 //lcd.noDisplay()();
 time1 = millis();
}
else if (x < 600){
 //hw 103 
//LEFT
lcd.display();
hw103(); //function plant soilmoisture
lcd.clear();
lcd.setCursor(0,0);
lcd.print("Soil Humidity:");
lcd.setCursor(0,1);
lcd.print(soilMoisture);
lcd.setCursor(3,1);
lcd.print("%");
//delay(delayDisplay);
//lcd.noDisplay()();
time1 = millis();
}
else if (x < 800){
lcd.display();
//SELECT
 lcd.clear();
  lcd.setCursor(0,0);
  lcd.print("Tank-E:");
  lcd.setCursor(7,0);
  lcd.print(tankfill3);
  lcd.setCursor(10,0);
  lcd.print("%");
  time1 = millis();
}




 
}//end loop

 

void ph() {

for(int i=0;i<10;i++) 
 { 
  buf[i]=analogRead(analogInPin);
  delay(10);
 }
 for(int i=0;i<9;i++)
 {
  for(int j=i+1;j<10;j++)
  {
   if(buf[i]>buf[j])
   {
    temp=buf[i];
    buf[i]=buf[j];
    buf[j]=temp;
   }
  }
 }
 avgValue=0;
 for(int i=2;i<8;i++)
 {
 avgValue+=buf[i];
 }
 float pHVol=(float)avgValue*5.0/1024/6;
 phValue = -5.70 * pHVol + 21.34;
 Serial.print("ph = ");
 Serial.println(phValue);
 }

 
void hcsr1(){
 for(int i=0;i<10;i++) 
 {
  digitalWrite(trigPin1, LOW);// Clears the trigPin
  delayMicroseconds(2);

digitalWrite(trigPin1, HIGH);// Sets the trigPin on HIGH state for 10 micro seconds
delayMicroseconds(10);
digitalWrite(trigPin1, LOW);


  buf1[i]= pulseIn(echoPin1, HIGH);// Reads the echoPin, returns the sound wave travel time in microseconds 
  delay(delayHcsr);
 }
 for(int i=0;i<9;i++)
 {
  for(int j=i+1;j<10;j++)
  {
   if(buf1[i]>buf1[j])
   {
    temp=buf1[i];
    buf1[i]=buf1[j];
    buf1[j]=temp;
   }
  }
 }
 avgValue1=0;
 for(int i=2;i<8;i++)
 {
 avgValue1+=buf1[i];
 }
 float distance1 =(float)avgValue1*0.034/2/6;
Serial.print("Distance1 C: ");// Prints the distance on the Serial Monitor
Serial.println(distance1); 
x =distance1/27*100;
tankfill1 = 100-x;
Serial.print("percentage fill1 C: ");
Serial.print(tankfill1); 
Serial.println("%");
}//END HCSR1

void hcsr2(){
  
 for(int i=0;i<10;i++) 
 {
  digitalWrite(trigPin2, LOW);// Clears the trigPin
delayMicroseconds(2);
digitalWrite(trigPin2, HIGH);// Sets the trigPin on HIGH state for 10 micro seconds
delayMicroseconds(10);
digitalWrite(trigPin2, LOW);
buf2[i]= pulseIn(echoPin2, HIGH);// Reads the echoPin, returns the sound wave travel time in microseconds 
  delay(10);
 }
 for(int i=0;i<9;i++)
 {
  for(int j=i+1;j<10;j++)
  {
   if(buf2[i]>buf2[j])
   {
    temp=buf2[i];
    buf2[i]=buf2[j];
    buf2[j]=temp;    
   }
  }
 }
 avgValue2=0;
 for(int i=2;i<8;i++)
 {
 avgValue2+=buf2[i];
 }
 float distance2 =(float)avgValue2*0.034/2/6;
Serial.print("Distance2: ");// Prints the distance on the Serial Monitor
Serial.println(distance2); 
 x =distance2/27*100;
tankfill2 = 100-x;

Serial.print("percentage fill: ");
Serial.print(tankfill2); 
Serial.println("%");
}//HCSR2


void hcsr3(){
  
for(int i=0;i<10;i++) 
 {
digitalWrite(trigPin3, LOW);// Clears the trigPin
delayMicroseconds(2);

digitalWrite(trigPin3, HIGH);// Sets the trigPin on HIGH state for 10 micro seconds
delayMicroseconds(10);
digitalWrite(trigPin3, LOW);


  buf3[i]= pulseIn(echoPin3, HIGH);// Reads the echoPin, returns the sound wave travel time in microseconds 
  delay(10);
 }
 for(int i=0;i<9;i++)
 {
  for(int j=i+1;j<10;j++)
  {
   if(buf3[i]>buf3[j])
   {
  temp=buf3[i];
  buf3[i]=buf3[j];
  buf3[j]=temp;    
   }
  }
 }
 avgValue3=0;
 for(int i=2;i<8;i++)
 {
 avgValue3+=buf3[i];
 }
 float distance3 =(float)avgValue3*0.034/2/6;
Serial.print("Distance3: ");// Prints the distance on the Serial Monitor
Serial.println(distance3); 
 z =distance3/27*100;
tankfill3 = 100-z;

Serial.print("percentage fill: ");
Serial.print(tankfill3); 
Serial.println("%");

}//HCSR3
void hw103(){

for(int i=0;i<10;i++) 
 { 
  buf4[i]=analogRead(analogHw);
  delay(10);
 }
 for(int i=0;i<9;i++)
 {
  for(int j=i+1;j<10;j++)
  {
   if(buf4[i]>buf4[j])
   {
    temp=buf4[i];
    buf4[i]=buf4[j];
    buf4[j]=temp;
   }
  }
 }
 avgValue4=0;
 for(int i=2;i<8;i++)
 {
 avgValue4+=buf4[i];
 }
 float hwValue=(float)avgValue4/6;
 v = hwValue/1024*100;
 soilMoisture = 100-v;
 Serial.print("Moisture = ");
 Serial.print(soilMoisture);
 Serial.println("%");
 }
 

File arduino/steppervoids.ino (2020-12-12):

 void steppermotor(){
  lcd.clear();
  lcd.setCursor(0,0);
  lcd.print("StepperMotor");
if(digitalRead(enablePin)==HIGH){
  pinMode(enablePin,LOW);
}
// Set motor direction COUNTER clockwise
    lcd.setCursor(0,1);
  lcd.print("Right");
    digitalWrite(dirPin, HIGH);
  for(int x = 0; x < axisStep; x++){
      digitalWrite(stepPin, LOW);
    delayMicroseconds(stepdelay);
     digitalWrite(stepPin, HIGH);
    delayMicroseconds(stepdelay);
   
  }
    lcd.setCursor(0,1);
    lcd.print("       ");
  lcd.setCursor(0,1);
  lcd.print("Left");
  digitalWrite(dirPin, LOW);
  
  for(int x = 0; x <axisStep; x++){
     digitalWrite(stepPin, LOW);
    delayMicroseconds(stepdelay);
     digitalWrite(stepPin, HIGH);
    delayMicroseconds(stepdelay);
    
  
  }
  delay(1000);



  }
  void stepperhome(){
     digitalWrite(enablePin,LOW);
    lcd.clear();
  lcd.setCursor(0,0);
  lcd.print("StepperHome");
   lcd.setCursor(0,1);
  lcd.print("Right");
     digitalWrite(dirPin, LOW);
  while(digitalRead(endstop)== HIGH){
      digitalWrite(stepPin, LOW);
    delayMicroseconds(stepdelay);
     digitalWrite(stepPin, HIGH);
    delayMicroseconds(stepdelay);
   
  }
   lcd.setCursor(0,1);
    lcd.print("       ");
  lcd.setCursor(0,1);
  lcd.print("Left");
  digitalWrite(dirPin, HIGH);
  
  for(int x = 0; x < 100; x++){
     digitalWrite(stepPin, LOW);
    delayMicroseconds(stepdelay);
     digitalWrite(stepPin, HIGH);
    delayMicroseconds(stepdelay);
    
  
  }
  delay(1000);
     digitalWrite(enablePin,HIGH);
 }

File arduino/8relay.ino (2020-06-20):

int Relay1 = 45; 
int Relay2 = 46;
int Relay3 = 47;
int Relay4 = 48;
int Relay5 = 49;
int Relay6 = 50;
int Relay7 = 51;
int Relay8 = 52; 
void setup() {
pinMode(Relay1 , OUTPUT);
pinMode(Relay2 , OUTPUT);
pinMode(Relay3 , OUTPUT);
pinMode(Relay4 , OUTPUT);
pinMode(Relay5 , OUTPUT);
pinMode(Relay6 , OUTPUT);
pinMode(Relay7 , OUTPUT);
pinMode(Relay8 , OUTPUT);
}

void loop() {
 digitalWrite(Relay1 , LOW);
 delay(1000); 
 digitalWrite(Relay1 , HIGH);
 delay(1000); 
 
 digitalWrite(Relay2 , LOW);
 delay(1000); 
 digitalWrite(Relay2 , HIGH);
 delay(1000); 
 
 digitalWrite(Relay3 , LOW);
 delay(1000); 
 digitalWrite(Relay3 , HIGH);
 delay(1000); 
 
 digitalWrite(Relay4 , LOW);
 delay(1000); 
 digitalWrite(Relay4 , HIGH);
 delay(1000); 
 
 digitalWrite(Relay5 , LOW);
 delay(1000); 
 digitalWrite(Relay5 , HIGH);
 delay(1000); 

 digitalWrite(Relay6 , LOW);
 delay(1000); 
 digitalWrite(Relay6 , HIGH);
 delay(1000); 

 digitalWrite(Relay7 , LOW);
 delay(1000); 
 digitalWrite(Relay7 , HIGH);
 delay(1000); 

 digitalWrite(Relay8 , LOW);
 delay(1000); 
 digitalWrite(Relay8 , HIGH);
 delay(1000); 
 }
